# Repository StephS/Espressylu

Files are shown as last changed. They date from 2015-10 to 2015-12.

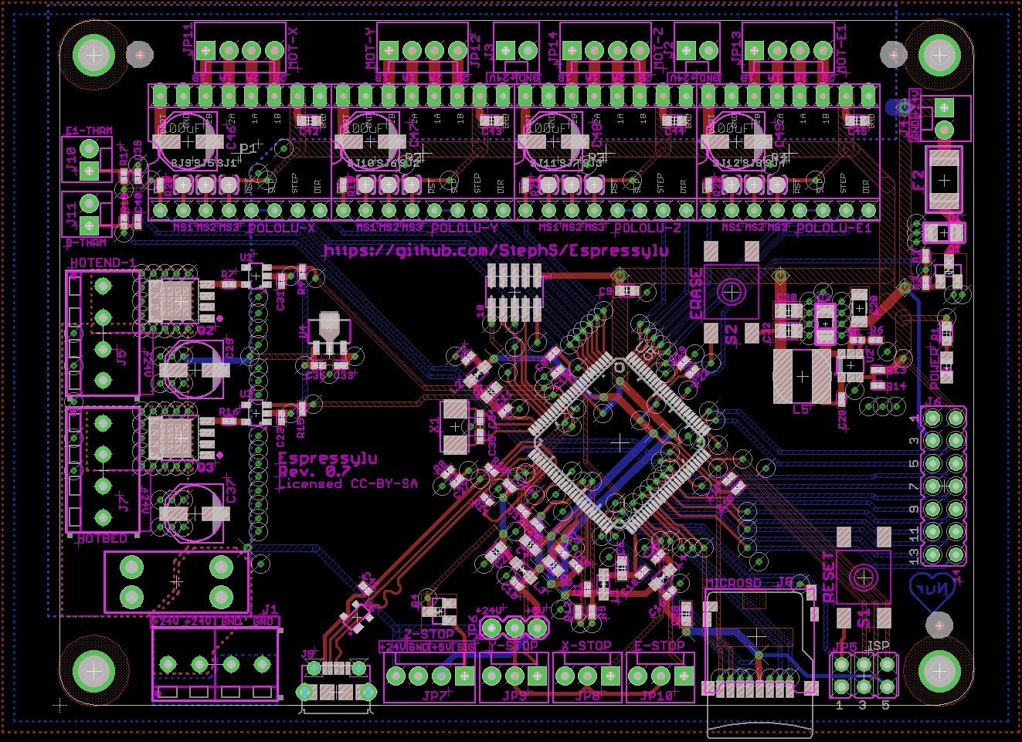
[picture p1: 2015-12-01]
Espressylu-0.7_Board.jpg

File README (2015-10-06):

This is a preliminary design for a 32bit control board, based on the Atmel SAM3A Microcontroller.
A few features:
4 Layer construction
Designed for 24v Operation
Native MicroSD
Polulu style stepper motor controllers

This board is designed for 24v operation only. A 20v OVLO is enabled on the main voltage regulator to prevent 12v operation. Because of this I removed any 12v power supply connectors.
The Hotbed, Hotend, Fan and Z Probe all have 24v connections. The Z Endstop uses a 4 pin configuration instead of a 3 pin. The extra pin supplies 24v for use with additional probes. Please be sure your probe can use 24v, or use an adapter with a 12v regulator to supply the normal 12v for the probe.

Since this version (version 0.6) is preliminary, I do not recommend its use until the design can be verified.
A BOM and PIN Mapping will be developed and shared as the design matures.

If you'd like to donate so I can buy the full version of Eagle, and make more cool stuff, please contact me through Google+ at https://plus.google.com/+StephanieS3D

Disclaimer:
These designs are provided without any warrenty, expressed or implied. This is a prototype designed for hobbiest use only.
Care should be taken during use and appropriate safety precautions taken.
The author is providing this item "as is". The author does not provide any warranty of the item whatsoever, whether express, implied, or statutory, including, but not limited to, any warranty of merchantability or fitness for a particular purpose or any warranty that the contents of the item will be error-free.
In no respect shall the author incur any liability for any damages, including, but limited to, direct, indirect, special, or consequential damages arising out of, resulting from, or any way connected to the use of the item, whether or not based upon warranty, contract, tort, or otherwise; whether or not injury was sustained by persons or property or otherwise; and whether or not loss was sustained from, or arose out of, the results of, the item, or any services that may be provided by the author.

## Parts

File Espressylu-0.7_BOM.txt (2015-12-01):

Part   Value                 Device                     Package             Description                          CURRENT DCR  DESCRIPTION                               ESR    IRMS MANUFACTURER            MANUFACTURER_PART_NUMBER NOTES                                                                       RDS_ON  REVERSE_VOLTAGE TOLERANCE VDC  VGS   VOLTAGE
C1     0.1uF                 CAPACITOR_0402             CAPC1005X60N                                                                                                                Samsung                 CL05A104KQ5NNNC                                                                                                              10%       6.3V              
C2     0.1uF                 CAPACITOR_0402             CAPC1005X60N                                                                                                                Samsung                 CL05A104KQ5NNNC                                                                                                              10%       6.3V              
C3     4.7uF                 CAPACITOR_0603             CAPC1608X92N                                                                                                                Samsung                 CL10B475KQ8NQNC                                                                                                              10%       6.3V              
C4     4.7uF                 CAPACITOR_0603             CAPC1608X92N                                                                                                                Samsung                 CL10B475KQ8NQNC                                                                                                              10%       6.3V              
C5     0.1uF                 CAPACITOR_0402             CAPC1005X60N                                                                                                                Samsung                 CL05A104KQ5NNNC                                                                                                              10%       6.3V              
C6     4.7uF                 CAPACITOR_0603             CAPC1608X92N                                                                                                                Samsung                 CL10B475KQ8NQNC                                                                                                              10%       6.3V              
C7     4.7uF                 CAPACITOR_0603             CAPC1608X92N                                                                                                                Samsung                 CL10B475KQ8NQNC                                                                                                              10%       6.3V              
C8     0.1uF                 CAPACITOR_0402             CAPC1005X60N                                                                                                                Samsung                 CL05A104KQ5NNNC                                                                                                              10%       6.3V              
C9     4.7uF                 CAPACITOR_0603             CAPC1608X92N                                                                                                                Samsung                 CL10B475KQ8NQNC                                                                                                              10%       6.3V              
C10    0.1uF                 CAPACITOR_0402             CAPC1005X60N                                                                                                                Samsung                 CL05A104KQ5NNNC                                                                                                              10%       6.3V              
C11    0.1uF                 CAPACITOR_0402             CAPC1005X60N                                                                                                                Samsung                 CL05A104KQ5NNNC                                                                                                              10%       6.3V              
C12    0.1uF                 CAPACITOR_0402             CAPC1005X60N                                                                                                                Samsung                 CL05A104KQ5NNNC                                                                                                              10%       6.3V              
C13    0.1uF                 CAPACITOR_0402             CAPC1005X60N                                                                                                                Samsung                 CL05A104KQ5NNNC                                                                                                              10%       6.3V              
C14    0.1uF                 CAPACITOR_0402             CAPC1005X60N                                                                                                                Samsung                 CL05A104KQ5NNNC                                                                                                              10%       6.3V              
C15    0.1uF                 CAPACITOR_0402             CAPC1005X60N                                                                                                                Samsung                 CL05A104KQ5NNNC                                                                                                              10%       6.3V              
C16    0.1uF                 CAPACITOR_0402             CAPC1005X60N                                                                                                                Samsung                 CL05A104KQ5NNNC                                                                                                              10%       6.3V              
C17    0.1uF                 CAPACITOR_0402             CAPC1005X60N                                                                                                                Samsung                 CL05A104KQ5NNNC                                                                                                              10%       6.3V              
C18    0.1uF                 CAPACITOR_0402             CAPC1005X60N                                                                                                                Samsung                 CL05A104KQ5NNNC                                                                                                              10%       6.3V              
C19    0.1uF                 CAPACITOR_0402             CAPC1005X60N                                                                                                                Samsung                 CL05A104KQ5NNNC                                                                                                              10%       6.3V              
C20    4.7uF                 CAPACITOR_1206             CAPC3215X168N                                                                                                               Yaiyo Yuden             UMK316AB7475KL-T                                                                                                             10%       50v               
C21    4.7uF                 CAPACITOR_0603             CAPC1608X92N                                                                                                                Samsung                 CL10B475KQ8NQNC                                                                                                              10%       6.3V              
C22    0.1uF                 CAPACITOR_0402             CAPC1005X60N                                                                                                                Samsung                 CL05A104KQ5NNNC                                                                                                              10%       6.3V              
C23    0.1uF                 CAPACITOR_0402             CAPC1005X60N                                                                                                                                                                                                                                                                     20%       50V               
C24    0.1uF                 CAPACITOR_0402             CAPC1005X60N                                                                                                                Samsung                 CL05A104KQ5NNNC                                                                                                              10%       6.3V              
C25    0.1uF                 CAPACITOR_0402             CAPC1005X60N                                                                                                                Samsung                 CL05A104KQ5NNNC                                                                                                              10%       6.3V              
C26    0.1uF                 CAPACITOR_0402             CAPC1005X60N                                                                                                                Samsung                 CL05A104KQ5NNNC                                                                                                              10%       6.3V              
C27    10pF                  CAPACITOR_0402             CAPC1005X60N                                                                                                                Samsung                 CL10C100JB8NCNC                                                                                                              5%        50V               
C28    0.1uF                 CAPACITOR_0402             CAPC1005X60N                                                                                                                Samsung                 CL10B104KB8NNNC                                                                                                              10%       50V               
C29    100uF                 CPOL-USD                   PANASONIC_D         POLARIZED CAPACITOR, American symbol                                                                    Panasonic               EEE-FTH101XAP                                                                                                                20%       50v               
C30    10uF                  CAPACITOR_0805             CAPC2012X145AN                                                                                                  0.0030      Murata                  GRM21BR71A106KE51L                                                                                                           10%       10v               
C31    0.1uF                 CAPACITOR_0402             CAPC1005X60N                                                                                                                                                                                                                                                                     20%       50V               
C32    10uF                  CAPACITOR_0805             CAPC2012X145AN                                                                                                  0.0030      Murata                  GRM21BR71A106KE51L                                                                                                           10%       10v               
C33    1uF                   CAPACITOR_0402             CAPC1005X60N                                                                                                                                                                                                                                                                     20%       50V               
C34    15pF                  CAPACITOR_0402             CAPC1005X60N                                                                                                                Samsung                 CL05C150JB5NNNC                                                                                                              5%        50V               
C35    15pF                  CAPACITOR_0402             CAPC1005X60N                                                                                                                Samsung                 CL05C150JB5NNNC                                                                                                              5%        50V               
C36    0.1uF                 CAPACITOR_0402             CAPC1005X60N                                                                                                                                                                                                                                                                     20%       50V               
C37    100uF                 CPOL-USD                   PANASONIC_D         POLARIZED CAPACITOR, American symbol                                                                    Panasonic               EEE-FTH101XAP                                                                                                                20%       50v               
C38    4.7uF                 CAPACITOR_0603             CAPC1608X92N                                                                                                                Samsung                 CL10B475KQ8NQNC                                                                                                              10%       6.3V              
C39    10uF                  CAPACITOR_0402             CAPC1005X60N                                                                                                                Murata                  GRM188R61C106MA73D                                                                                                           20%       16V               
C40    10uF                  CAPACITOR_0402             CAPC1005X60N                                                                                                                Murata                  GRM188R61C106MA73D                                                                                                           20%       16V               
C41    0.1uF                 CAPACITOR_0402             CAPC1005X60N                                                                                                                Murata                  GRM188R71C104KA01D                                                                                                           10%       16V               
C42    4.7uF                 CAPACITOR_0603             CAPC1608X92N                                                                                                                Samsung                 CL10B475KQ8NQNC                                                                                                              10%       6.3V              
C43    4.7uF                 CAPACITOR_0603             CAPC1608X92N                                                                                                                Samsung                 CL10B475KQ8NQNC                                                                                                              10%       6.3V              
C44    4.7uF                 CAPACITOR_0603             CAPC1608X92N                                                                                                                Samsung                 CL10B475KQ8NQNC                                                                                                              10%       6.3V              
C45    4.7uF                 CAPACITOR_0603             CAPC1608X92N                                                                                                                Samsung                 CL10B475KQ8NQNC                                                                                                              10%       6.3V              
C46    100uF                 CPOL-USD                   PANASONIC_D         POLARIZED CAPACITOR, American symbol                                                                    Panasonic               EEE-FTH101XAP                                                                                                                20%       50v               
C47    100uF                 CPOL-USD                   PANASONIC_D         POLARIZED CAPACITOR, American symbol                                                                    Panasonic               EEE-FTH101XAP                                                                                                                20%       50v               
C48    100uF                 CPOL-USD                   PANASONIC_D         POLARIZED CAPACITOR, American symbol                                                                    Panasonic               EEE-FTH101XAP                                                                                                                20%       50v               
C49    100uF                 CPOL-USD                   PANASONIC_D         POLARIZED CAPACITOR, American symbol                                                                    Panasonic               EEE-FTH101XAP                                                                                                                20%       50v               
D1     SCH-DIODESOD123F      SCH-DIODESOD123F           SOD123F             Schottky Diodes                      1A                                                                 NXP Semiconductors      PMEG4010CEH,115                                                                                              40V                                         
D2     SCH-DIODESOD123F      SCH-DIODESOD123F           SOD123F             Schottky Diodes                      1A                                                                 NXP Semiconductors      PMEG4010CEH,115                                                                                              40V                                         
F1     MINI-FUSEMINI-FUSE    MINI-FUSEMINI-FUSE         MINI_FUSE                                                15A                                                                Keystone                3568                                                                                                                                                     
F2     MINISMDC050F1812      MINISMDC050F1812           MINISMDC                                                 0.5A                                                               TE Connectivity         MINISMDC050F-2                                                                                                                                           
J1     4P-TERM-BLOCK284391-4 4P-TERM-BLOCK284391-4      284391-4                                                 12A                                                                TE Connectivity         284391-4                                                                                                                                                 
J2     M02POLAR              M02POLAR                   MOLEX-1X2           Header 2                                          CONN HEADER 2POS .100 VERT TIN                        Molex                   0022272021               Can use alternative part for Right Angle. MFG: TE Connectivity PN: 640455-2                                                     
J3     M02POLAR              M02POLAR                   MOLEX-1X2           Header 2                                          CONN HEADER 2POS .100 VERT TIN                        Molex                   0022272021               Can use alternative part for Right Angle. MFG: TE Connectivity PN: 640455-2                                                     
J4     M02POLAR              M02POLAR                   MOLEX-1X2           Header 2                                          CONN HEADER 2POS .100 VERT TIN                        Molex                   0022272021               Can use alternative part for Right Angle. MFG: TE Connectivity PN: 640455-2                                                     
J5     HOTEND-1              4P-TERM-BLOCK284391-4      284391-4                                                 12A                                                                TE Connectivity         284391-4                                                                                                                                                 
J6     2x7                   JP7Q                       JP7Q                JUMPER                                            DIL VERTICAL PC TAIL PIN HEADER                       Harwin                  M20-9980746                                                                                                                                              
J7     HOTBED                4P-TERM-BLOCK284391-4      284391-4                                                 12A                                                                TE Connectivity         284391-4                                                                                                                                                 
J8     MICROSD               MICROSD                    AMPHENOL-MICROSD                                                      CONN MICRO SD CARD PUSH-PULL R/A                      Amphenol                114-00841-68                                                                                                                                             
J9     USB-MICRO-PTH         USB-MICRO-PTH              USB-MICROB-PTH      USB Connectors                                                                                          FCI                     10118194-0001LF                                                                                                                                          
J10    M02POLAR              M02POLAR                   MOLEX-1X2           Header 2                                          CONN HEADER 2POS .100 VERT TIN                        Molex                   0022272021               Can use alternative part for Right Angle. MFG: TE Connectivity PN: 640455-2                                                     
J11    M02POLAR              M02POLAR                   MOLEX-1X2           Header 2                                          CONN HEADER 2POS .100 VERT TIN                        Molex                   0022272021               Can use alternative part for Right Angle. MFG: TE Connectivity PN: 640455-2                                                     
JP1    FIDUCIAL1X2.5         FIDUCIAL1X2.5              FIDUCIAL-1X2.5      Fiducial Alignment Points                                                                                                                                                                                                                                                                
JP2    FIDUCIAL1X2.5         FIDUCIAL1X2.5              FIDUCIAL-1X2.5      Fiducial Alignment Points                                                                                                                                                                                                                                                                
JP3    FIDUCIAL1X2.5         FIDUCIAL1X2.5              FIDUCIAL-1X2.5      Fiducial Alignment Points                                                                                                                                                                                                                                                                
JP4    JTAG-HEADER           JTAG-HEADER                2X05-0.5-SMD                                                          CONN HEADER 10POS DL UNSHRD SMD                       FCI                     20021121-00010C4LF                                                                                                                                       
JP5    ISP                   PROGHEADER                 ISP                 JUMPER                                                                                                                                                                                                                                                                                   
JP6    JUMPER-3PTH           JUMPER-3PTH                1X03                                                                                                                                                                                                                                                                                                         
JP7    Z-STOP                M04POLAR                   MOLEX-1X4           Header 4                                          CONN HEADER 4POS .100 VERT TIN                        Molex                   0022272041               Can use alternative part for Right Angle. MFG: TE Connectivity PN: 640455-4                                                     
JP8    M03POLAR              M03POLAR                   MOLEX-1X3           Header 3                                          CONN HEADER 3POS .100 VERT TIN                        Molex                   0022272031               Can use alternative part for Right Angle. MFG: TE Connectivity PN: 640455-3                                                     
JP9    M03POLAR              M03POLAR                   MOLEX-1X3           Header 3                                          CONN HEADER 3POS .100 VERT TIN                        Molex                   0022272031               Can use alternative part for Right Angle. MFG: TE Connectivity PN: 640455-3                                                     
JP10   M03POLAR              M03POLAR                   MOLEX-1X3           Header 3                                          CONN HEADER 3POS .100 VERT TIN                        Molex                   0022272031               Can use alternative part for Right Angle. MFG: TE Connectivity PN: 640455-3                                                     
JP11   MOT-X                 M04POLAR                   MOLEX-1X4           Header 4                                          CONN HEADER 4POS .100 VERT TIN                        Molex                   0022272041               Can use alternative part for Right Angle. MFG: TE Connectivity PN: 640455-4                                                     
JP12   MOT-Y                 M04POLAR                   MOLEX-1X4           Header 4                                          CONN HEADER 4POS .100 VERT TIN                        Molex                   0022272041               Can use alternative part for Right Angle. MFG: TE Connectivity PN: 640455-4                                                     
JP13   MOT-E1                M04POLAR                   MOLEX-1X4           Header 4                                          CONN HEADER 4POS .100 VERT TIN                        Molex                   0022272041               Can use alternative part for Right Angle. MFG: TE Connectivity PN: 640455-4                                                     
JP14   MOT-Z                 M04POLAR                   MOLEX-1X4           Header 4                                          CONN HEADER 4POS .100 VERT TIN                        Molex                   0022272041               Can use alternative part for Right Angle. MFG: TE Connectivity PN: 640455-4                                                     
L1     MH2029-300Y           FERRITE_BEAD_0805          FERRITE_BEAD_0805   SMD EMI Suppression Ferrite Beads                 30 Ohm @ 100MHz                                       Bourns Inc              MH2029-300Y                                                                                                                                              
L2     MH2029-300Y           FERRITE_BEAD_0805          FERRITE_BEAD_0805   SMD EMI Suppression Ferrite Beads                 30 Ohm @ 100MHz                                       Bourns Inc              MH2029-300Y                                                                                                                                              
L3     MH2029-300Y           FERRITE_BEAD_0805          FERRITE_BEAD_0805   SMD EMI Suppression Ferrite Beads                 30 Ohm @ 100MHz                                       Bourns Inc              MH2029-300Y                                                                                                                                              
L4     MH2029-300Y           FERRITE_BEAD_0805          FERRITE_BEAD_0805   SMD EMI Suppression Ferrite Beads                 30 Ohm @ 100MHz                                       Bourns Inc              MH2029-300Y
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

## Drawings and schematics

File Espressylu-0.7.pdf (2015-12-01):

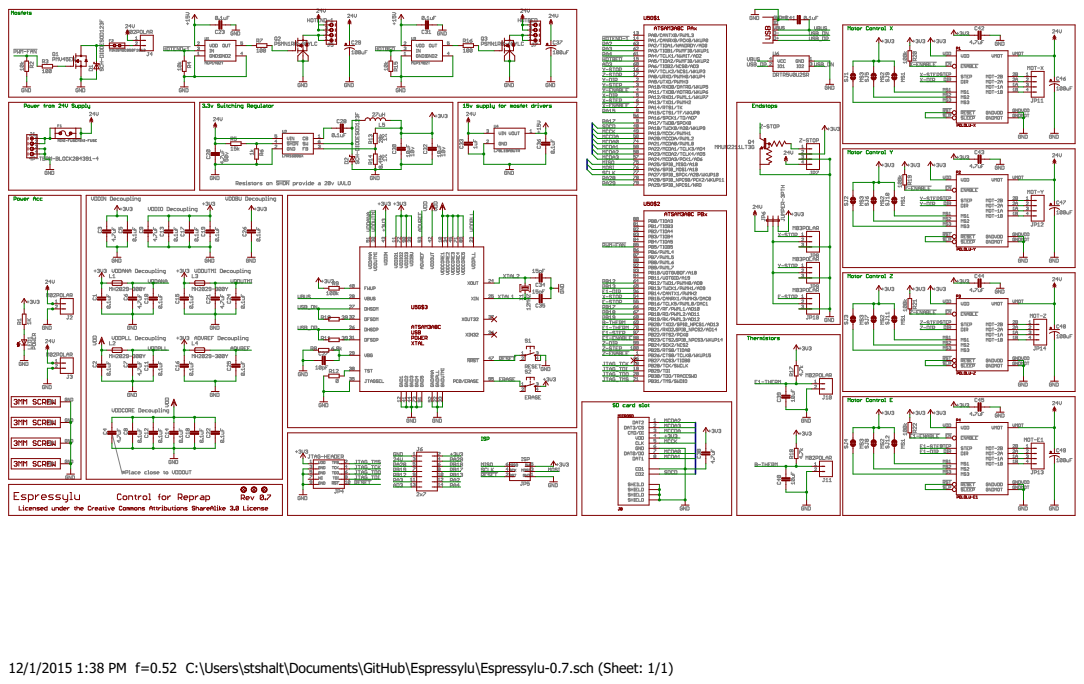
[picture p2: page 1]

12/1/2015 1:38 PM f=0.52 C:\Users\stshalt\Documents\GitHub\Espressylu\Espressylu-0.7.sch (Sheet: 1/1)

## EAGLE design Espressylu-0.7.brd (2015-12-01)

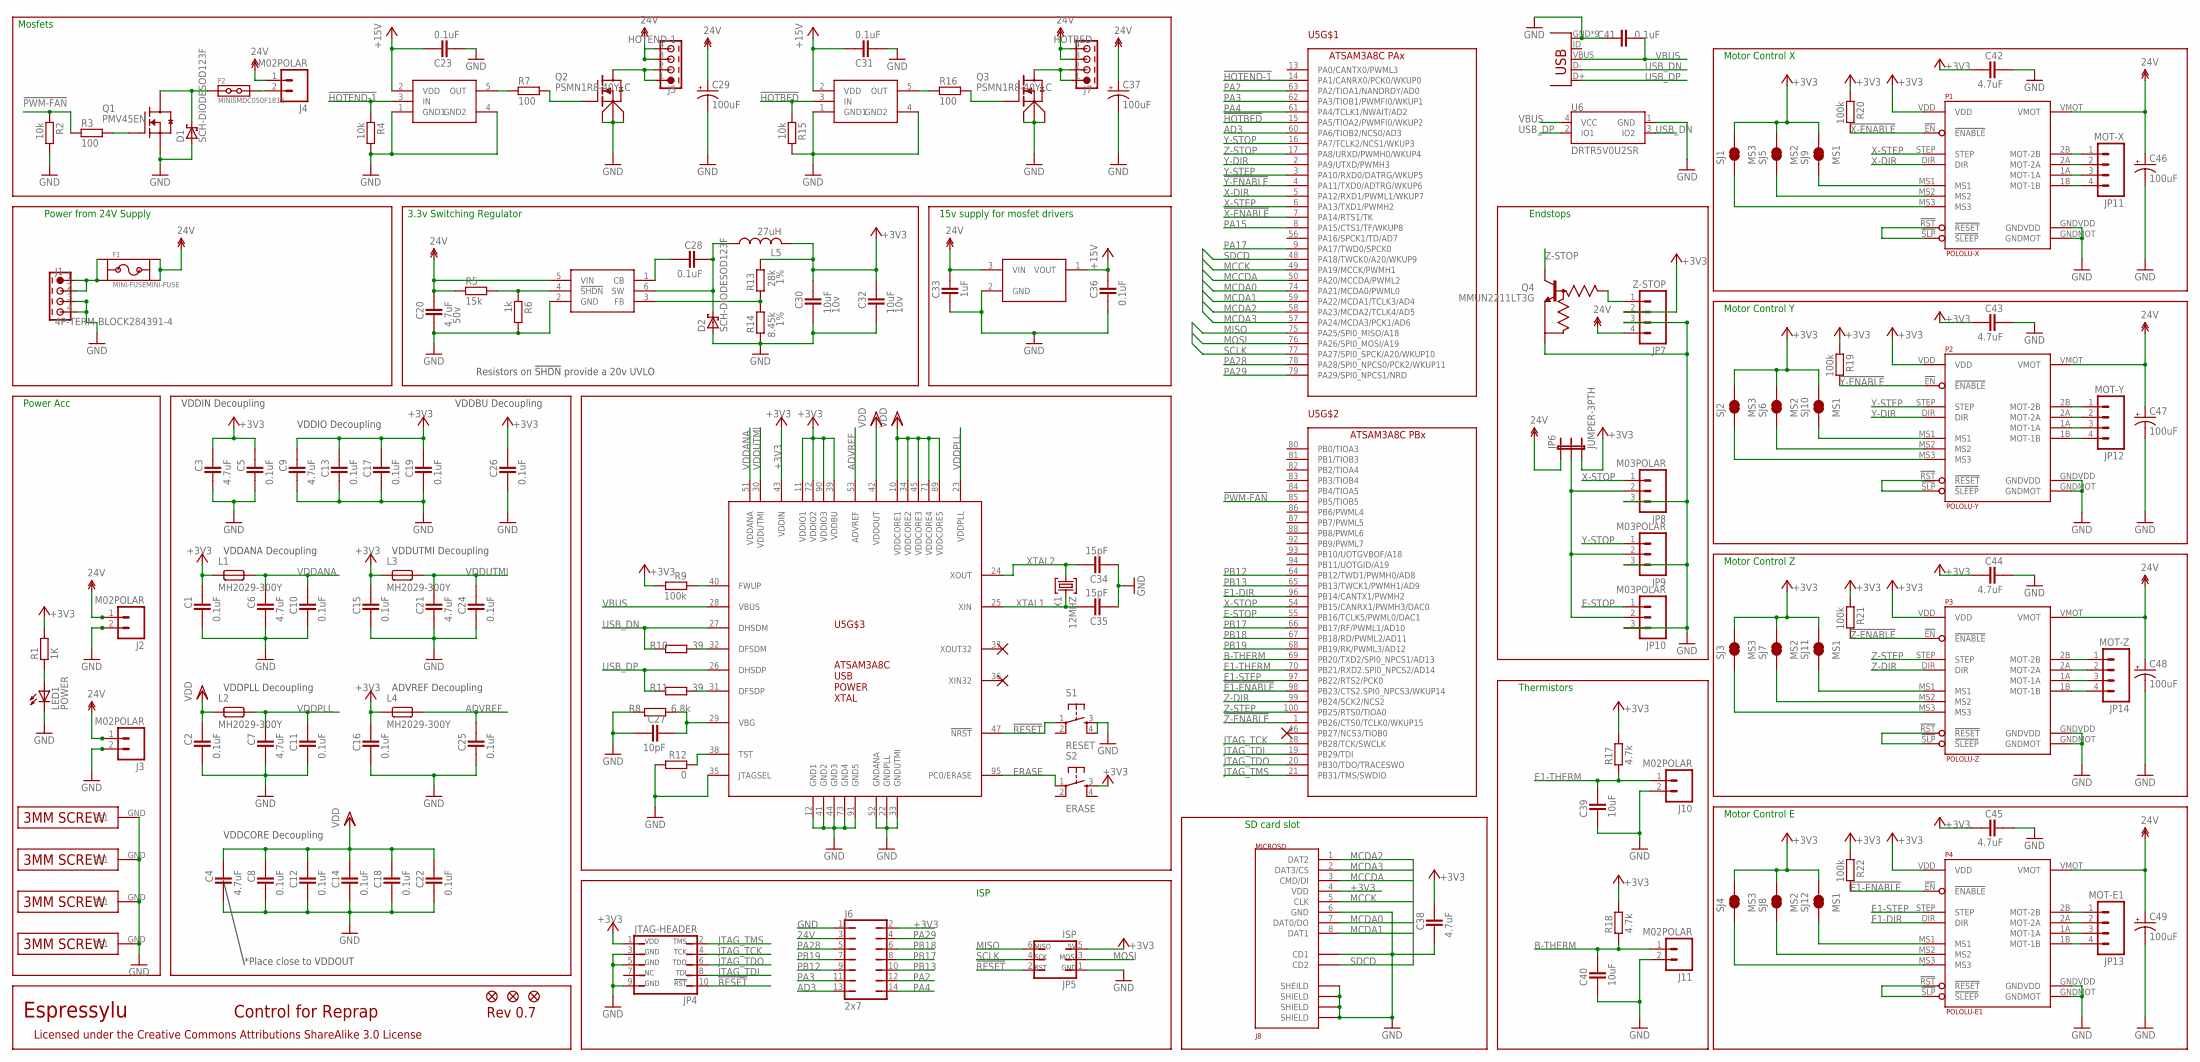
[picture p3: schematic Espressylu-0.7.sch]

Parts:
C1, C2, C5, C8, C10, C11, C12, C13, C14, C15, C16, C17, C18, C19, C22, C24, C25, C26: 0.1uF; CAPC1005X60N; TOLERANCE 10%; MANUFACTURER_PART_NUMBER CL05A104KQ5NNNC
C3, C4, C6, C7, C9, C21, C38, C42, C43, C44, C45: 4.7uF; CAPC1608X92N; TOLERANCE 10%; MANUFACTURER_PART_NUMBER CL10B475KQ8NQNC
C20: 4.7uF; CAPC3215X168N; TOLERANCE 10%; MANUFACTURER_PART_NUMBER UMK316AB7475KL-T
C23, C31, C36: 0.1uF; CAPC1005X60N; TOLERANCE 20%
C27: 10pF; CAPC1005X60N; TOLERANCE 5%; MANUFACTURER_PART_NUMBER CL10C100JB8NCNC
C28: 0.1uF; CAPC1005X60N; TOLERANCE 10%; MANUFACTURER_PART_NUMBER CL10B104KB8NNNC
C29, C37, C46, C47, C48, C49: 100uF; PANASONIC_D; TOLERANCE 20%; MANUFACTURER_PART_NUMBER EEE-FTH101XAP
C30, C32: 10uF; CAPC2012X145AN; TOLERANCE 10%; MANUFACTURER_PART_NUMBER GRM21BR71A106KE51L
C33: 1uF; CAPC1005X60N; TOLERANCE 20%
C34, C35: 15pF; CAPC1005X60N; TOLERANCE 5%; MANUFACTURER_PART_NUMBER CL05C150JB5NNNC
C39, C40: 10uF; CAPC1005X60N; TOLERANCE 20%; MANUFACTURER_PART_NUMBER GRM188R61C106MA73D
C41: 0.1uF; CAPC1005X60N; TOLERANCE 10%; MANUFACTURER_PART_NUMBER GRM188R71C104KA01D
D1: SCH-DIODESOD123F; SOD123F
D2: SCH-DIODESOD123F; SOD123F; MANUFACTURER_PART_NUMBER PMEG4010CEH,115
F1: MINI-FUSEMINI-FUSE; MINI_FUSE
F2: MINISMDC050F1812; MINISMDC
J1: 4P-TERM-BLOCK284391-4; 284391-4
J2, J3, J4, J10, J11: M02POLAR; MOLEX-1X2; MANUFACTURER_PART_NUMBER 0022272021
J5: HOTEND-1; 284391-4
J6: 2x7; JP7Q; MANUFACTURER_PART_NUMBER M20-9980746
J7: HOTBED; 284391-4
J8: MICROSD; AMPHENOL-MICROSD
J9: USB-MICRO-PTH; USB-MICROB-PTH
JP1, JP2, JP3: FIDUCIAL1X2.5; FIDUCIAL-1X2.5
JP4: JTAG-HEADER; 2X05-0.5-SMD
JP5: ISP
JP6: JUMPER-3PTH; 1X03
JP7: Z-STOP; MOLEX-1X4
JP8, JP9, JP10: M03POLAR; MOLEX-1X3; MANUFACTURER_PART_NUMBER 0022272031
JP11: MOT-X; MOLEX-1X4
JP12: MOT-Y; MOLEX-1X4
JP13: MOT-E1; MOLEX-1X4
JP14: MOT-Z; MOLEX-1X4
L1, L2, L3, L4: MH2029-300Y; FERRITE_BEAD_0805; MANUFACTURER_PART_NUMBER MH2029-300Y
L5: 27uH; SDR0604; MANUFACTURER_PART_NUMBER SDR0604-270YL
LED1: POWER; CHIPLED_0805; MANUFACTURER_PART_NUMBER APT2012SGC
P1: POLOLU-X; POLOLU-STEPPER-PTH
P2: POLOLU-Y; POLOLU-STEPPER-PTH
P3: POLOLU-Z; POLOLU-STEPPER-PTH
P4: POLOLU-E1; POLOLU-STEPPER-PTH
Q1: PMV45EN; SOT23C; VOLTAGE 60V; MANUFACTURER_PART_NUMBER IRLML2060TRPBF
Q2, Q3: PSMN1R8-40YLC; LFPACK-POWERPAK-SO8
Q4: MMUN2211LT3G; SOT23C; MANUFACTURER_PART_NUMBER MMUN2211LT3G
R1: 1K; RESC1608X55N
R2, R4, R15: 10k; RESC1005X40AN
R3, R7, R16: 100; RESC1005X40AN
R5: 15k; RESC1005X40AN
R6: 1k; RESC1005X40AN
R8: 6.8k; RESC1005X40AN; TOLERANCE 1%
R9, R19, R20, R21, R22: 100k; RESC1005X40AN
R10, R11: 39; RESC1005X40AN; TOLERANCE 1%
R12: 0; RESC1005X40AN
R13: 28k; RESC1005X40AN; TOLERANCE 1%
R14: 8.45k; RESC1005X40AN; TOLERANCE 1%
R17, R18: 4.7k; RESC1005X40AN
S1: RESET; SWITCH-SMD-4P
S2: ERASE; SWITCH-SMD-4P
SCREW1, SCREW2, SCREW3, SCREW4: 3MM-SCREW; PLATEDSCREW
SJ1, SJ2, SJ3, SJ4: MS3; SJ_2S-TRACE
SJ5, SJ6, SJ7, SJ8: MS2; SJ_2S-TRACE
SJ9, SJ10, SJ11, SJ12: MS1; SJ_2S-TRACE
U1, U3: MCP1402T; SOT23-5
U2: LMR16006X; TSOT6
U4: L78L15ABUTR; SOT89
U5: ATSAM3A8C-LQFP100; LQFP100
U6: DRTR5V0U2SR; SOT143-R
X1: 12MHZ; NDK-XTAL; MANUFACTURER_PART_NUMBER ABM3-12.000MHZ-B2-T

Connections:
5VREG_CB: C28.2, U2.1 (CB)
5VREG_FB: R13.2, R14.1, U2.3 (FB)
5VREG_SW: C28.1, D2.C, L5.1, U2.6 (SW)
12V_FUSE: F1.P$1, F1.P$2, J1.1, J1.2
24V: C20.1, C29.+, C33.1, C37.+, C46.+, C47.+, C48.+, C49.+, F1.P$3, F1.P$4, J2.1, J3.1, J4.1, J5.3, J5.4, J6.3, J7.3, J7.4, JP6.1, JP7.4, P1.VMOT, P2.VMOT, P3.VMOT, P4.VMOT, R5.1, U2.5 (VIN), U4.3 (VIN)
!E1-ENABLE: P4.!EN (!ENABLE), R22.2, U5.98 (PB23/CTS2.SPI0_NPCS3/WKUP14)
!HOTBED: R15.1, U3.3 (IN), U5.15 (PA5/TIOA2/PWMFI0/WKUP2)
!HOTEND-1: R4.1, U1.3 (IN), U5.14 (PA1/CANRX0/PCK0/WKUP0)
!PWM-FAN: R2.1, R3.1, U5.85 (PB5/TIOB5)
!RESET: JP4.10, JP5.2, S1.1, U5.47 (!NRST)
!X-ENABLE: P1.!EN (!ENABLE), R20.2, U5.7 (PA14/RTS1/TK)
!Y-ENABLE: P2.!EN (!ENABLE), R19.2, U5.4 (PA11/TXD0/ADTRG/WKUP6)
!Z-ENABLE: P3.!EN (!ENABLE), R21.2, U5.1 (PB26/CTS0/TCLK0/WKUP15)
+3V3: C1.1, C3.1, C5.1, C9.1, C13.1, C15.1, C16.1, C17.1, C19.1, C26.1, C30.1, C32.1, C38.1, C42.2, C43.2, C44.2, C45.2, J6.2, J8.4 (VDD), JP4.1, JP5.5, JP6.3, JP7.2, L1.1, L3.1, L4.1, L5.2, P1.VDD, P2.VDD, P3.VDD, P4.VDD, R1.2, R9.2, R13.1, R17.2, R18.2, R19.1, R20.1, R21.1, R22.1, S2.3, SJ1.2, SJ2.2, SJ3.2, SJ4.2, SJ5.2, SJ6.2, SJ7.2, SJ8.2, SJ9.2, SJ10.2, SJ11.2, SJ12.2, U5.11 (VDDIO1), U5.39 (VDDBU), U5.43 (VDDIN), U5.72 (VDDIO2), U5.90 (VDDIO3)
+15V: C23.1, C31.1, C36.1, U1.2 (VDD), U3.2 (VDD), U4.1 (VOUT)
AD3: J6.13, U5.60 (PA6/TIOB2/NCS0/AD3)
ADVREF: C25.1, L4.2, U5.53 (ADVREF)
B-THERM: C40.2, J11.1, R18.1, U5.69 (PB20/TXD2/SPI0_NPCS1/AD13)
E1-DIR: P4.DIR, U5.96 (PB14/CANTX1/PWMH2)
E1-STEP: P4.STEP, U5.97 (PB22/RTS2/PCK0)
E1-THERM: C39.2, J10.1, R17.1, U5.70 (PB21/RXD2.SPI0_NPCS2/AD14)
E-MOT-1A: JP13.3, P4.1A (MOT-1A)
E-MOT-1B: JP13.4, P4.1B (MOT-1B)
E-MOT-2A: JP13.2, P4.2A (MOT-2A)
E-MOT-2B: JP13.1, P4.2B (MOT-2B)
E-MS1: P4.MS1, SJ12.1
E-MS2: P4.MS2, SJ8.1
E-MS3: P4.MS3, SJ4.1
E-RESETSLEEP: P4.!RST (!RESET), P4.!SLP (!SLEEP)
E-STOP: JP10.1, U5.55 (PB16/TCLK5/PWML0/DAC1)
ENDSTOP+V: JP6.2, JP8.2, JP9.2, JP10.2
ERASE: S2.1, U5.95 (PC0/ERASE)
GND: C1.2, C2.2, C3.2, C4.2, C5.2, C6.2, C7.2, C8.2, C9.2, C10.2, C11.2, C12.2, C13.2, C14.2, C15.2, C16.2, C17.2, C18.2, C19.2, C20.2, C21.2, C22.2, C23.2, C24.2, C25.2, C26.2, C27.2, C29.-, C30.2, C31.2, C32.2, C33.2, C34.1, C35.1, C36.2, C37.-, C38.2, C39.1, C40.1, C41.1, C42.1, C43.1, C44.1, C45.1, C46.-, C47.-, C48.-, C49.-, D1.A, D2.A, J1.3, J1.4, J2.2, J3.2, J6.1, J8.6 (GND), J8.C1 (SHEILD), J8.C2 (SHIELD), J8.C3 (SHIELD), J8.C4 (SHIELD), J8.CD1, J9.GND, J9.GND1 (GND), J9.GND2 (GND), J9.GND3 (GND), J9.GND4 (GND), J9.GND5 (GND), J9.GND6 (GND), J9.GND7 (GND), J9.GND8 (GND), J10.2, J11.2, JP4.3, JP4.5, JP4.9, JP5.1, JP7.3, JP8.3, JP9.3, JP10.3, LED1.C, P1.GNDMOT, P1.GNDVDD, P2.GNDMOT, P2.GNDVDD, P3.GNDMOT, P3.GNDVDD, P4.GNDMOT, P4.GNDVDD, Q1.2 (S), Q2.1 (S1), Q2.2 (S2), Q2.3 (S3), Q3.1 (S1), Q3.2 (S2), Q3.3 (S3), Q4.2 (E), R2.2, R4.2, R6.2, R8.1, R12.2, R14.2, R15.2, S1.3, S1.4, SCREW1.GND, SCREW2.GND, SCREW3.GND, SCREW4.GND, U1.1 (GND1), U1.4 (GND2), U2.2 (GND), U3.1 (GND1), U3.4 (GND2), U4.2 (GND), U5.12 (GND1), U5.22 (GNDPLL), U5.33 (GNDUTMI), U5.35 (JTAGSEL), U5.41 (GND2), U5.44 (GND3), U5.52 (GNDANA), U5.73 (GND4), U5.91 (GND5), U6.1 (GND)
HOTBED-GND: J7.1, J7.2, Q3.5-8 (D)
HOTEND-GND: J5.1, J5.2, Q2.5-8 (D)
JTAG_TCK: JP4.4, U5.18 (PB28/TCK/SWCLK)
JTAG_TDI: JP4.8, U5.19 (PB29/TDI)
JTAG_TDO: JP4.6, U5.20 (PB30/TDO/TRACESWO)
JTAG_TMS: JP4.2, U5.21 (PB31/TMS/SWDIO)
MCCDA: J8.3 (CMD/DI), U5.50 (PA20/MCCDA/PWML2)
MCCK: J8.5 (CLK), U5.49 (PA19/MCCK/PWMH1)
MCDA0: J8.7 (DAT0/DO), U5.74 (PA21/MCDA0/PWML0)
MCDA1: J8.8 (DAT1), U5.59 (PA22/MCDA1/TCLK3/AD4)
MCDA2: J8.1 (DAT2), U5.58 (PA23/MCDA2/TCLK4/AD5)
MCDA3: J8.2 (DAT3/CS), U5.57 (PA24/MCDA3/PCK1/AD6)
MISO: JP5.6, U5.75 (PA25/SPI0_MISO/A18)
MOSI: JP5.3, U5.76 (PA26/SPI0_MOSI/A19)
unnamed: LED1.A, R1.1
unnamed: Q3.4 (G), R16.2
unnamed: R5.2, R6.1, U2.4 (!SHDN)
unnamed: R9.1, U5.40 (FWUP)
unnamed: F2.P$2, J4.2
unnamed: D1.C, F2.P$1, Q1.3 (D)
unnamed: R12.1, U5.38 (TST)
unnamed: R10.2, U5.32 (DFSDM)
unnamed: Q1.1 (G), R3.2
unnamed: Q2.4 (G), R7.2
unnamed: R11.2, U5.31 (DFSDP)
unnamed: R16.1, U3.5 (OUT)
unnamed: R7.1, U1.5 (OUT)
PA2: J6.12, U5.63 (PA2/TIOA1/NANDRDY/AD0)
PA3: J6.11, U5.62 (PA3/TIOB1/PWMFI0/WKUP1)
PA4: J6.14, U5.61 (PA4/TCLK1/NWAIT/AD2)
PA15: U5.8 (PA15/CTS1/TF/WKUP8)
PA17: U5.9 (PA17/TWD0/SPCK0)
PA28: J6.5, U5.78 (PA28/SPI0_NPCS0/PCK2/WKUP11)
PA29: J6.4, U5.79 (PA29/SPI0_NPCS1/NRD)
PB12: J6.9, U5.64 (PB12/TWD1/PWMH0/AD8)
PB13: J6.10, U5.65 (PB13/TWCK1/PWMH1/AD9)
PB17: J6.8, U5.66 (PB17/RF/PWML1/AD10)
PB18: J6.6, U5.67 (PB18/RD/PWML2/AD11)
PB19: J6.7, U5.68 (PB19/RK/PWML3/AD12)
SCLK: JP5.4, U5.77 (PA27/SPI0_SPCK/A20/WKUP10)
SDCD: J8.CD2, U5.48 (PA18/TWCK0/A20/WKUP9)
USB_DN: J9.D-, R10.1, U5.27 (DHSDM), U6.3 (IO2)
USB_DP: J9.D+, R11.1, U5.26 (DHSDP), U6.2 (IO1)
VBG: C27.1, R8.2, U5.29 (VBG)
VBUS: C41.2, J9.VBUS, U5.28 (VBUS), U6.4 (VCC)
VDD: C2.1, C4.1, C8.1, C12.1, C14.1, C18.1, C22.1, L2.1, U5.10 (VDDCORE1), U5.34 (VDDCORE2), U5.42 (VDDOUT), U5.45 (VDDCORE3), U5.71 (VDDCORE4), U5.89 (VDDCORE5)
VDDANA: C6.1, C10.1, L1.2, U5.51 (VDDANA)
VDDPLL: C7.1, C11.1, L2.2, U5.23 (VDDPLL)
VDDUTMI: C21.1, C24.1, L3.2, U5.30 (VDDUTMI)
X-DIR: P1.DIR, U5.5 (PA12/RXD1/PWML1/WKUP7)
X-MOT-1A: JP11.3, P1.1A (MOT-1A)
X-MOT-1B: JP11.4, P1.1B (MOT-1B)
X-MOT-2A: JP11.2, P1.2A (MOT-2A)
X-MOT-2B: JP11.1, P1.2B (MOT-2B)
X-MS1: P1.MS1, SJ9.1
X-MS2: P1.MS2, SJ5.1
X-MS3: P1.MS3, SJ1.1
X-RESETSLEEP: P1.!RST (!RESET), P1.!SLP (!SLEEP)
X-STEP: P1.STEP, U5.6 (PA13/TXD1/PWMH2)
X-STOP: JP8.1, U5.54 (PB15/CANRX1/PWMH3/DAC0)
XTAL1: C35.2, U5.25 (XIN), X1.P$2 (2)
XTAL2: C34.2, U5.24 (XOUT), X1.P$1 (1)
Y-DIR: P2.DIR, U5.2 (PA9/UTXD/PWMH3)
Y-MOT-1A: JP12.3, P2.1A (MOT-1A)
Y-MOT-1B: JP12.4, P2.1B (MOT-1B)
Y-MOT-2A: JP12.2, P2.2A (MOT-2A)
Y-MOT-2B: JP12.1, P2.2B (MOT-2B)
Y-MS1: P2.MS1, SJ10.1
Y-MS2: P2.MS2, SJ6.1
Y-MS3: P2.MS3, SJ2.1
Y-RESETSLEEP: P2.!RST (!RESET), P2.!SLP (!SLEEP)
Y-STEP: P2.STEP, U5.3 (PA10/RXD0/DATRG/WKUP5)
Y-STOP: JP9.1, U5.16 (PA7/TCLK2/NCS1/WKUP3)
Z-DIR: P3.DIR, U5.99 (PB24/SCK2/NCS2)
Z-MOT-1A: JP14.3, P3.1A (MOT-1A)
Z-MOT-1B: JP14.4, P3.1B (MOT-1B)
Z-MOT-2A: JP14.2, P3.2A (MOT-2A)
Z-MOT-2B: JP14.1, P3.2B (MOT-2B)
Z-MS1: P3.MS1, SJ11.1
Z-MS2: P3.MS2, SJ7.1
Z-MS3: P3.MS3, SJ3.1
Z-RESETSLEEP: P3.!RST (!RESET), P3.!SLP (!SLEEP)
Z-STEP: P3.STEP, U5.100 (PB25/RTS0/TIOA0)
Z-STOP: Q4.3 (C), U5.17 (PA8/URXD/PWMH0/WKUP4)
Z-STOP-BIAS: JP7.1, Q4.1 (B)

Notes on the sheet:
Motor Control X
Motor Control Y
Motor Control Z
Motor Control E
ISP
Thermistors
Endstops
Mosfets
Power Acc
Espressylu
Rev 0.7
Control for Reprap
Licensed under the Creative Commons Attributions ShareAlike 3.0 License
15v supply for mosfet drivers
Power from 24V Supply
3.3v Switching Regulator
SD card slot
VDDCORE Decoupling
VDDIN Decoupling
VDDPLL Decoupling
VDDIO Decoupling
VDDANA Decoupling
VDDUTMI Decoupling
*Place close to VDDOUT
VDDBU Decoupling
ADVREF Decoupling
Resistors on !SHDN! provide a 20v UVLO

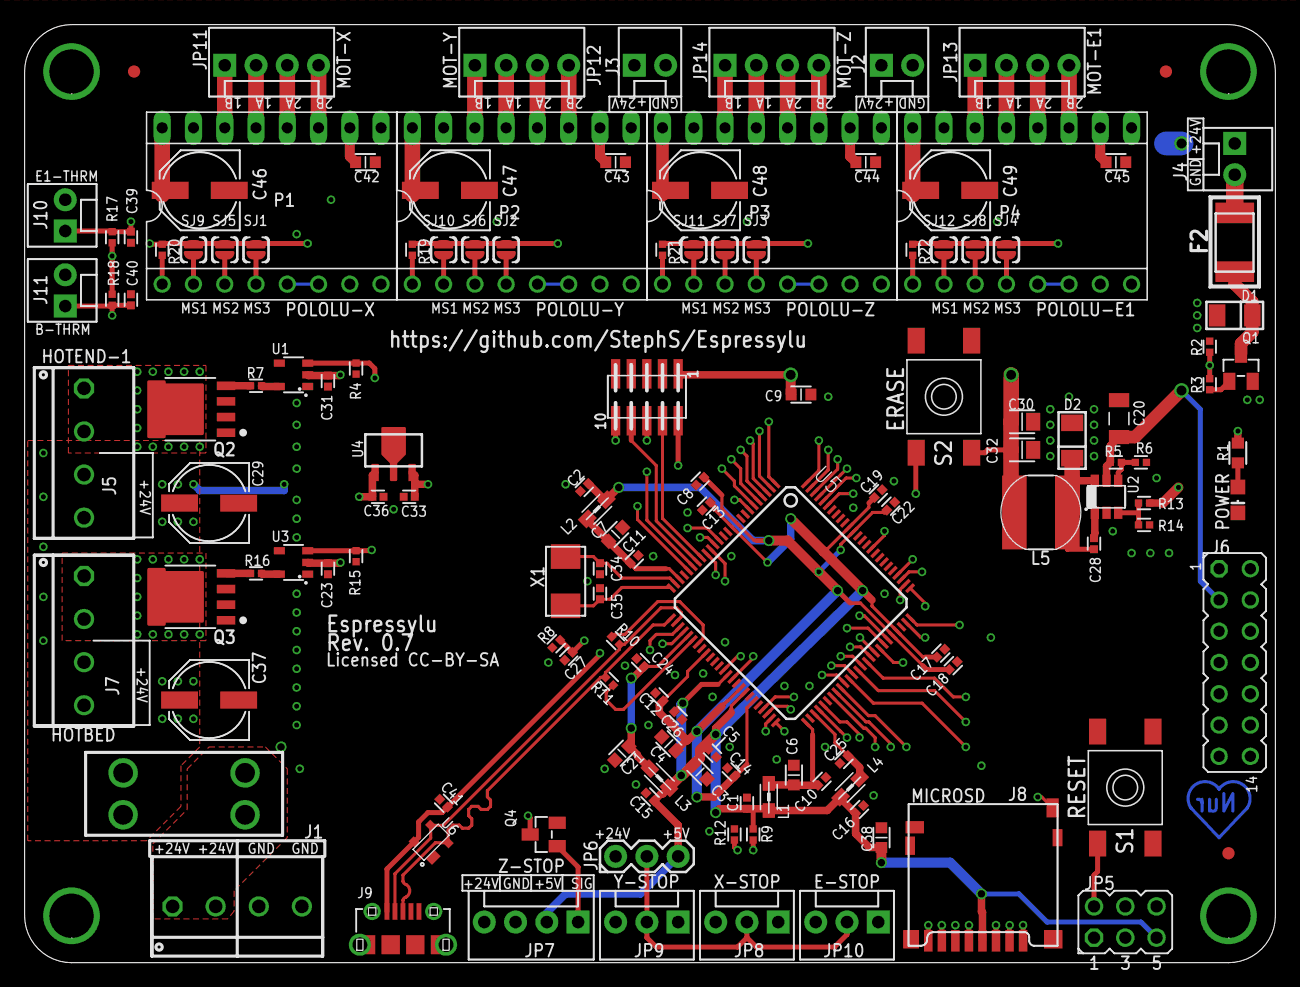
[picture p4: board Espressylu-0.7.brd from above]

Board: 4 copper layers, 101.6 x 76.2 mm, 139 parts (0 on the bottom side), 116 nets.

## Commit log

2015-10-06 First public revision 0.6
    Preliminary design, not recommended for manufacturing.
    [Espressylu-0.6.brd, Espressylu-0.6.sch]
2015-10-06 Adding board layout picture
2015-10-07 Layout cleanup
    Moved the stepper motor headers closer to the connectors. Cleaned up the
    schematic and labels.
    [Espressylu-0.6.brd, Espressylu-0.6.sch]
2015-12-01 Cleaned up Silkscreen and added caps
    I cleaned up the silkscreen for all of the components.
    Capacitors were added to the motor driver VCC pins.
    More GND Vias were added to reduce noise.
    The mosfets were shifted away from the connectors slightly.
    The stepper motor connectors were shifted slightly closer to the edge of
    the board.
    All of the HV pins are labelled as 24v. This board should only be used
    with 24v.
    [Espressylu-0.7.brd, Espressylu-0.7.sch]

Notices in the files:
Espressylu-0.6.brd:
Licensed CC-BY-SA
